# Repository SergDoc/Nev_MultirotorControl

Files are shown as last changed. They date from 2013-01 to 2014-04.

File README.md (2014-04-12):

Nev_MultirotorControl
=====================
Baseflight (naze32) port to own STM32F4 board

STM32F407VGT6

MPU6000 on SPI

HMC5883

MS5611

50x50mm 2 layer pcb, 45mm mounting pattern 

8 + 12 PWM I/O  input or output for RC/CPPM/Motors/Servos 

8 channel standard PWM RC input 

PWM (50..1kHz) motor output for up to 12 motors, 8 motors + 4 Servos

Onboard USB connector 

3 UART accessible for telemetry,  firmware update,  Spektrum Satellite RX or GPS

Battery voltage monitoring and low-voltage alarm 

Buzzer for alarm/user notification 

4 Status LEDs

2 VDD & VCC Status LEDs



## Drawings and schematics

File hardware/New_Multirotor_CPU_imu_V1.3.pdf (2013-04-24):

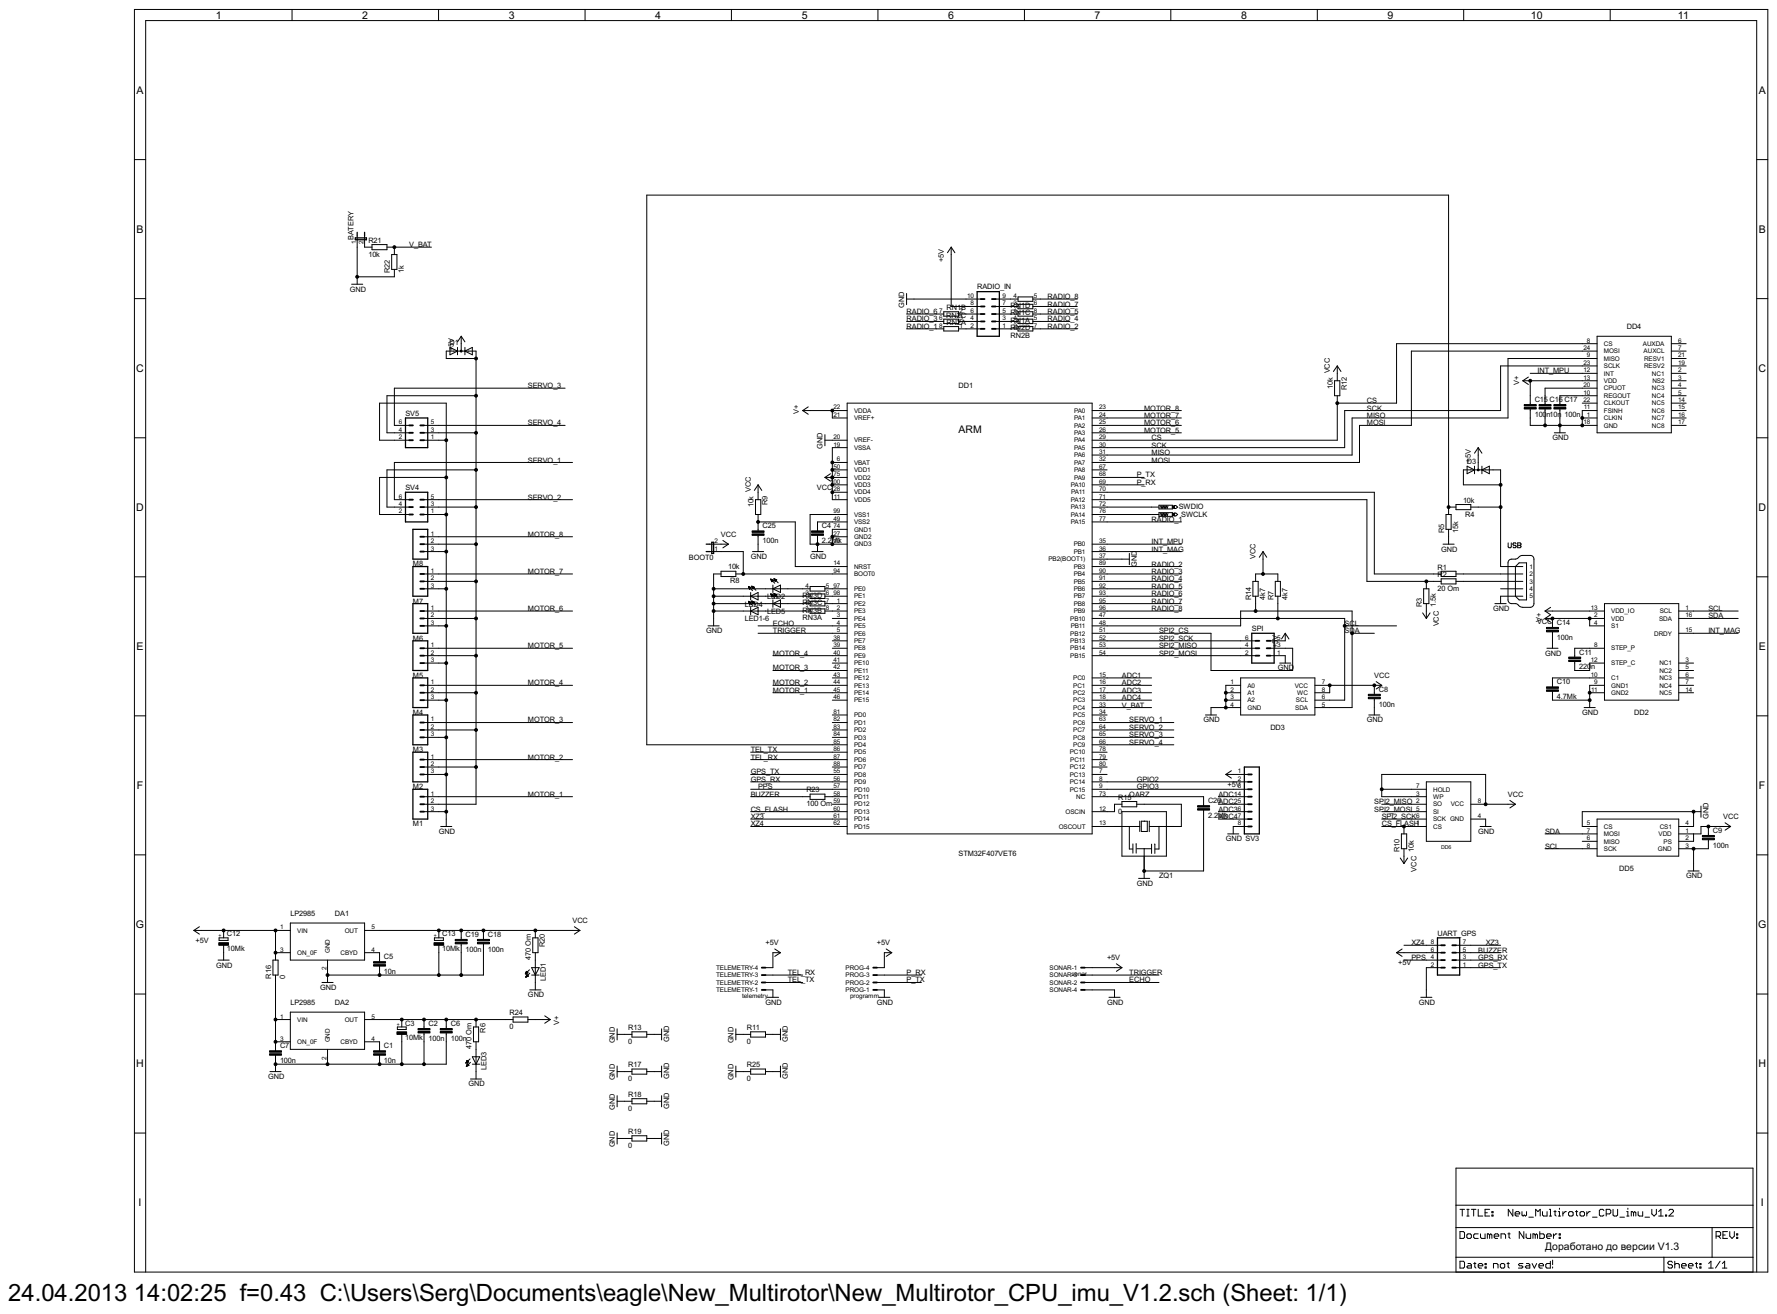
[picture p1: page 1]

C4 | 76 PA15 77 PB0 RADIO_1 35 PB1 INT_MPU

52 PB14 SPI2_MISO | 4 | 3
53 PB15 SPI2_MOSI | 2

PROG-1 PROG-2 PROG-3 PROG-4

24.04.2013 14:02:25 f=0.43 C:\Users\Serg\Documents\eagle\New_Multirotor\New_Multirotor_CPU_imu_V1.2.sch (Sheet: 1/1)

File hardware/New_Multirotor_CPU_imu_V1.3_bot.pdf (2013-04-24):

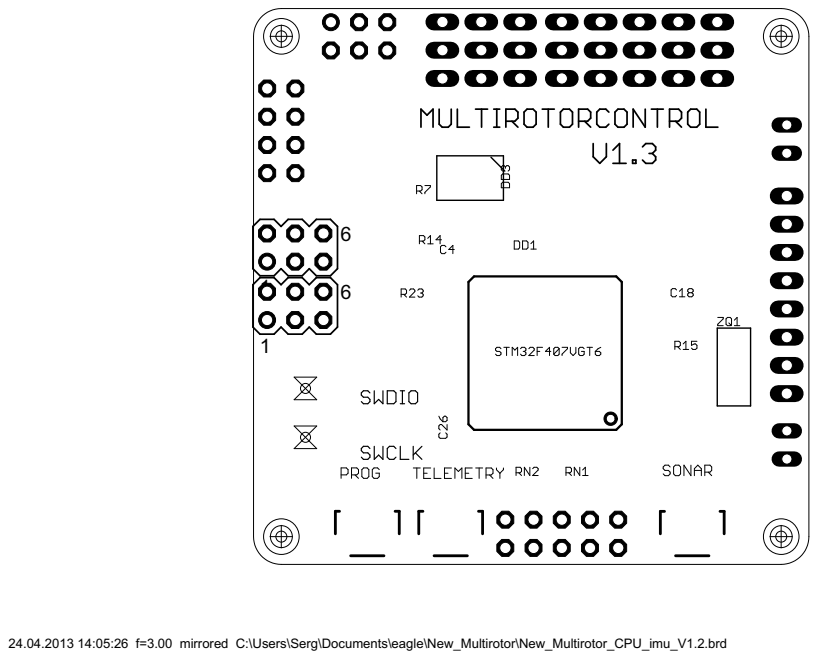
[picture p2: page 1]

24.04.2013 14:05:26 f=3.00 mirrored C:\Users\Serg\Documents\eagle\New_Multirotor\New_Multirotor_CPU_imu_V1.2.brd

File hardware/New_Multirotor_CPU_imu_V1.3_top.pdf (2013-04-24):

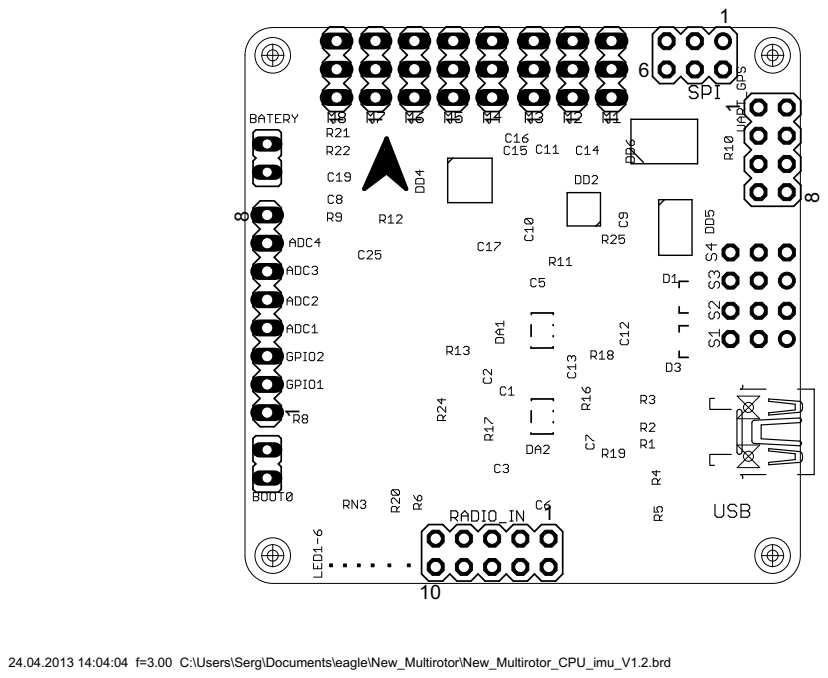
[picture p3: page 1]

24.04.2013 14:04:04 f=3.00 C:\Users\Serg\Documents\eagle\New_Multirotor\New_Multirotor_CPU_imu_V1.2.brd

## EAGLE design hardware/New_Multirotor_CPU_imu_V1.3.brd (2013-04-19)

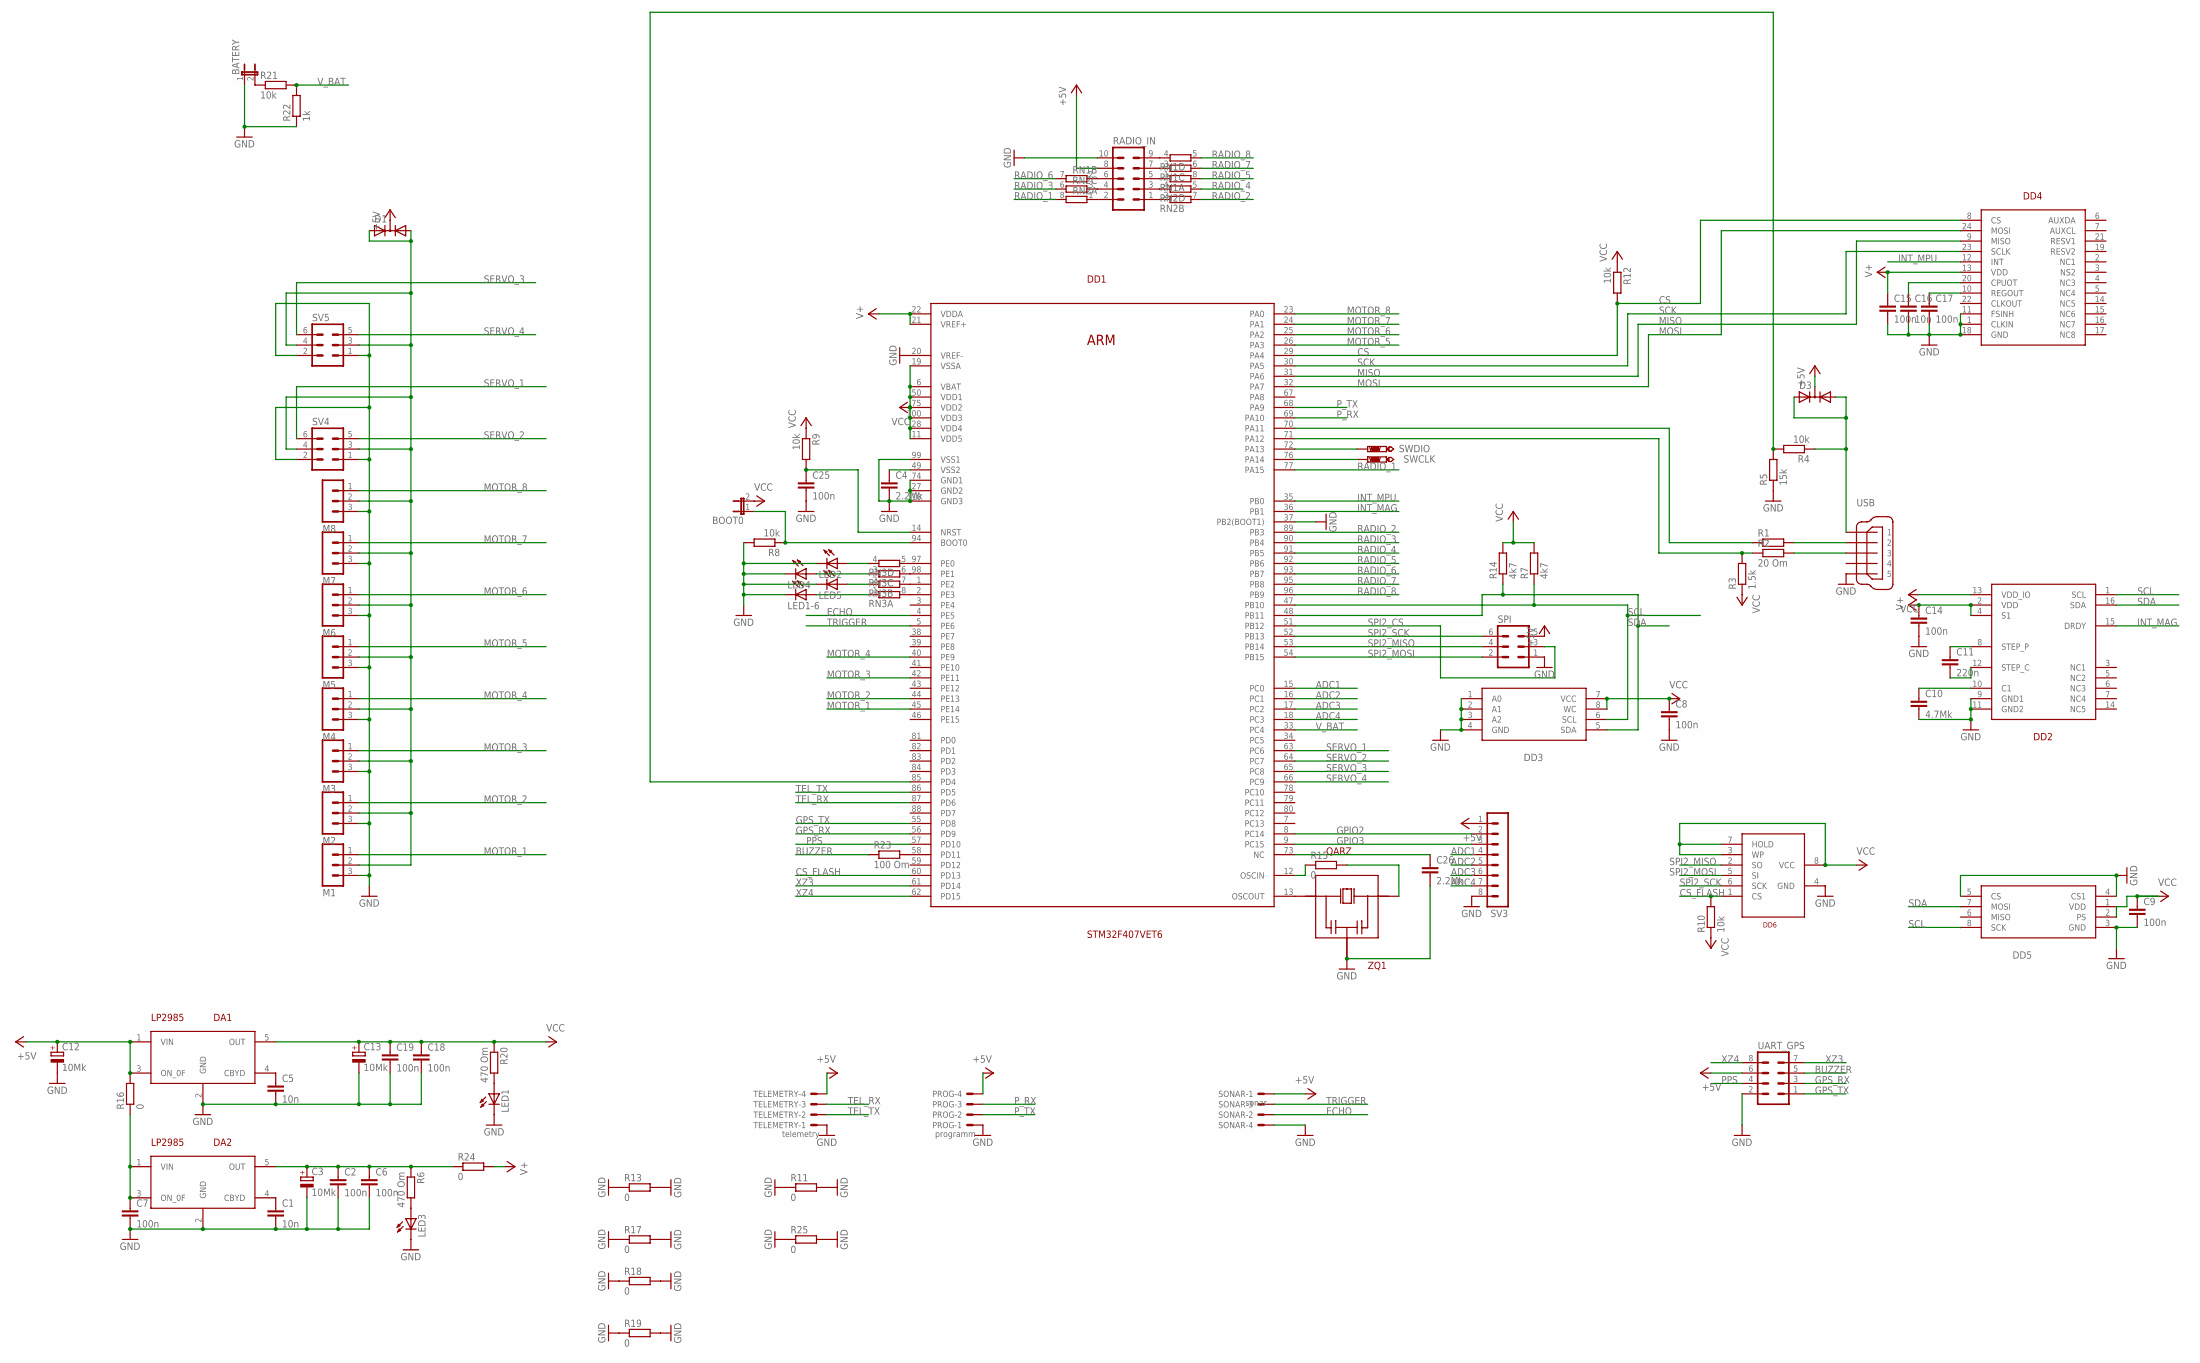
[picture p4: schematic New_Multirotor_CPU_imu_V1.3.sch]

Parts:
BATERY: JP1E; JP1
BOOT0: JP1E; JP1
C1, C5, C16: 10n; C0603K
C2, C6, C7, C8, C9, C14, C15, C17, C18, C19, C25: 100n; C0603K
C3, C12, C13: 10Mk; A/3216-18W
C4, C26: 2.2Mk; C0603K
C10: 4.7Mk; C0603K
C11: 220n; C0603K
D1, D3: DIODE-2AC|CASOT23; SOT23
DA1, DA2: LP2985; SOT23-5L
DD1: STM32F407VET6; LQFP100
DD2: HMC5883L; LCC-16
DD3: 24C512; SOIC8
DD4: MPU6000; JEDEC
DD5: MS5611-01BA03
DD6: W25X40; SOIC8
LED1, LED1-6, LED2, LED3, LED4, LED5: LEDCHIPLED_0603; CHIPLED_0603
M1, M2, M3, M4, M5, M6, M7, M8: MA03-1
PROG: programm; SM04B-SRSS-TB
R1: R-EU_R0603; R0603
R2: 20 Om; R0603
R3: 1.5k; R0603
R4, R8, R9, R10, R12, R21: 10k; R0603
R5: 15k; R0603
R6, R20: 470 Om; R0603
R7, R14: 4k7; R0603
R11, R13, R15, R16, R17, R18, R19, R24, R25: 0; R0603
R22: 1k; R0603
R23: 100 Om; R0603
RADIO_IN: MA05-2
RN1, RN2, RN3: 4R-N0603-ARV; 0603-ARV
SONAR: sonar; SM04B-SRSS-TB
SPI: MA03-2
SV3: MA08-1
SV4, SV5: MA03-2
SWCLK: PTR1TP12R; TP12R
SWDIO: PTR1TP12R; TP12R
TELEMETRY: telemetry; SM04B-SRSS-TB
UART_GPS: MA04-2
USB: 32005-201
ZQ1: QARZ

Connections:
+5V: C12.+, D1.3 (C), D3.3 (C), DA1.1 (VIN), DA1.3 (ON_0F), PROG.4, R16.2, RADIO_IN.8, SONAR.1, SPI.5, SV3.1, TELEMETRY.4, UART_GPS.6
ADC1: DD1.15 (PC0), SV3.4
ADC2: DD1.16 (PC1), SV3.5
ADC3: DD1.17 (PC2), SV3.6
ADC4: DD1.18 (PC3), SV3.7
BUZZER: R23.1, UART_GPS.5
CS: DD1.29 (PA4), DD4.8 (CS), R12.2
CS_FLASH: DD1.60 (PD13), DD6.1 (CS), R10.2
ECHO: DD1.4 (PE5), SONAR.2
GND: BATERY.1, C1.2, C2.2, C3.-, C4.2, C5.2, C6.2, C7.2, C8.2, C9.2, C10.2, C12.-, C13.-, C14.2, C15.2, C16.2, C17.2, C18.2, C19.2, C25.2, C26.2, DA1.2 (GND), DA2.2 (GND), DD1.10 (GND3), DD1.20 (VREF-), DD1.27 (GND2), DD1.37 (PB2(BOOT1)), DD1.74 (GND1), DD1.99 (VSS1), DD2.9 (GND1), DD2.11 (GND2), DD3.1 (A0), DD3.2 (A1), DD3.3 (A2), DD3.4 (GND), DD4.1 (CLKIN), DD4.11 (FSINH), DD4.18 (GND), DD5.3 (GND), DD5.4 (CS1), DD5.5 (CS), DD6.4 (GND), LED1.C, LED1-6.C, LED2.C, LED3.C, LED4.C, LED5.C, M1.3, M2.3, M3.3, M4.3, M5.3, M6.3, M7.3, M8.3, PROG.1, R5.1, R8.2, R11.1, R11.2, R13.1, R13.2, R17.1, R17.2, R18.1, R18.2, R19.1, R19.2, R22.1, R25.1, R25.2, RADIO_IN.10, SONAR.4, SPI.1, SV3.8, SV4.1, SV4.2, SV5.1, SV5.2, TELEMETRY.1, UART_GPS.2, USB.5, ZQ1.2
GPIO2: DD1.8 (PC14), SV3.2
GPIO3: DD1.9 (PC15), SV3.3
GPS_RX: DD1.56 (PD9), UART_GPS.3
GPS_TX: DD1.55 (PD8), UART_GPS.1
INT_MAG: DD1.36 (PB1), DD2.15 (DRDY)
INT_MPU: DD1.35 (PB0), DD4.12 (INT)
MISO: DD1.31 (PA6), DD4.9 (MISO)
MOSI: DD1.32 (PA7), DD4.24 (MOSI)
MOTOR_1: DD1.45 (PE14), M1.1
MOTOR_2: DD1.44 (PE13), M2.1
MOTOR_3: DD1.42 (PE11), M3.1
MOTOR_4: DD1.40 (PE9), M4.1
MOTOR_5: DD1.26 (PA3), M5.1
MOTOR_6: DD1.25 (PA2), M6.1
MOTOR_7: DD1.24 (PA1), M7.1
MOTOR_8: DD1.23 (PA0), M8.1
unnamed: DD1.13 (OSCOUT), ZQ1.1
unnamed: R15.2, ZQ1.3
unnamed: DD1.97 (PE0), RN3.5 (2)
unnamed: C1.1, DA2.4 (CBYD)
unnamed: DD1.98 (PE1), RN3.6 (2)
unnamed: LED3.A, R6.2
unnamed: C2.1, C3.+, C6.1, DA2.5 (OUT), R6.1, R24.1
unnamed: RADIO_IN.5, RN1.1
unnamed: C7.1, DA2.1 (VIN), DA2.3 (ON_0F), R16.1
unnamed: DD1.1 (PE2), RN3.7 (2)
unnamed: DD1.2 (PE3), RN3.8 (2)
unnamed: DD1.12 (OSCIN), R15.1
unnamed: LED1.A, R20.2
unnamed: DD1.72 (PA13), SWDIO.TP
unnamed: DD1.76 (PA14), SWCLK.TP
unnamed: LED2.A, RN3.4 (1)
unnamed: LED4.A, RN3.3 (1)
unnamed: C16.1, DD4.20 (CPUOT)
unnamed: D1.1 (A1), D1.2 (A2), M1.2, M2.2, M3.2, M4.2, M5.2, M6.2, M7.2, M8.2, SV4.3, SV4.4, SV5.3, SV5.4
unnamed: RADIO_IN.3, RN2.4 (1)
unnamed: C17.1, DD4.10 (REGOUT)
unnamed: RADIO_IN.9, RN1.4 (1)
unnamed: RADIO_IN.7, RN1.3 (1)
unnamed: BATERY.2, R21.1
unnamed: C10.1, DD2.10 (C1)
unnamed: C11.2, DD2.12 (STEP_C)
unnamed: C11.1, DD2.8 (STEP_P)
unnamed: DD1.58 (PD11), R23.2
unnamed: RADIO_IN.6, RN1.2 (1)
unnamed: RADIO_IN.1, RN2.2 (1)
unnamed: RADIO_IN.4, RN2.3 (1)
unnamed: RADIO_IN.2, RN2.1
unnamed: LED5.A, RN3.2 (1)
unnamed: LED1-6.A, RN3.1
unnamed: DD1.70 (PA11), R1.1
unnamed: DD1.71 (PA12), R2.1, R3.2
unnamed: R1.2, USB.2
unnamed: R2.2, USB.3
unnamed: DD1.85 (PD4), R4.2, R5.2
unnamed: D3.1 (A1), D3.2 (A2), R4.1, USB.1
unnamed: C5.1, DA1.4 (CBYD)
unnamed: C4.1, DD1.49 (VSS2)
unnamed: BOOT0.1, DD1.94 (BOOT0), R8.1
unnamed: C25.1, DD1.14 (NRST), R9.2
unnamed: C26.1, DD1.73 (NC)
PPS: DD1.57 (PD10), UART_GPS.4
P_RX: DD1.69 (PA10), PROG.3
P_TX: DD1.68 (PA9), PROG.2
RADIO_1: DD1.77 (PA15), RN2.8 (2)
RADIO_2: DD1.89 (PB3), RN2.7 (2)
RADIO_3: DD1.90 (PB4), RN2.6 (2)
RADIO_4: DD1.91 (PB5), RN2.5 (2)
RADIO_5: DD1.92 (PB6), RN1.8 (2)
RADIO_6: DD1.93 (PB7), RN1.7 (2)
RADIO_7: DD1.95 (PB8), RN1.6 (2)
RADIO_8: DD1.96 (PB9), RN1.5 (2)
SCK: DD1.30 (PA5), DD4.23 (SCLK)
SCL: DD1.47 (PB10), DD2.1 (SCL), DD3.6 (SCL), DD5.8 (SCK), R7.1
SDA: DD1.48 (PB11), DD2.16 (SDA), DD3.5 (SDA), DD5.7 (MOSI), R14.1
SERVO_1: DD1.63 (PC6), SV4.6
SERVO_2: DD1.64 (PC7), SV4.5
SERVO_3: DD1.65 (PC8), SV5.6
SERVO_4: DD1.66 (PC9), SV5.5
SPI2_CS: DD1.51 (PB12), SPI.3
SPI2_MISO: DD1.53 (PB14), DD6.2 (SO), SPI.4
SPI2_MOSI: DD1.54 (PB15), DD6.5 (SI), SPI.2
SPI2_SCK: DD1.52 (PB13), DD6.6 (SCK), SPI.6
TEL_RX: DD1.87 (PD6), TELEMETRY.3
TEL_TX: DD1.86 (PD5), TELEMETRY.2
TRIGGER: DD1.5 (PE6), SONAR.3
V+: C14.1, C15.1, DD1.21 (VREF+), DD1.22 (VDDA), DD2.2 (VDD), DD2.4 (S1), DD4.13 (VDD), R24.2
VCC: BOOT0.2, C8.1, C9.1, C13.+, C18.1, C19.1, DA1.5 (OUT), DD1.6 (VBAT), DD1.11 (VDD5), DD1.19 (VSSA), DD1.28 (VDD4), DD1.50 (VDD1), DD1.75 (VDD2), DD1.100 (VDD3), DD2.13 (VDD_IO), DD3.7 (VCC), DD3.8 (WC), DD5.1 (VDD), DD5.2 (PS), DD6.3 (WP), DD6.7 (HOLD), DD6.8 (VCC), R3.1, R7.2, R9.1, R10.1, R12.1, R14.2, R20.1
V_BAT: DD1.33 (PC4), R21.2, R22.2
XZ3: DD1.61 (PD14), UART_GPS.7
XZ4: DD1.62 (PD15), UART_GPS.8

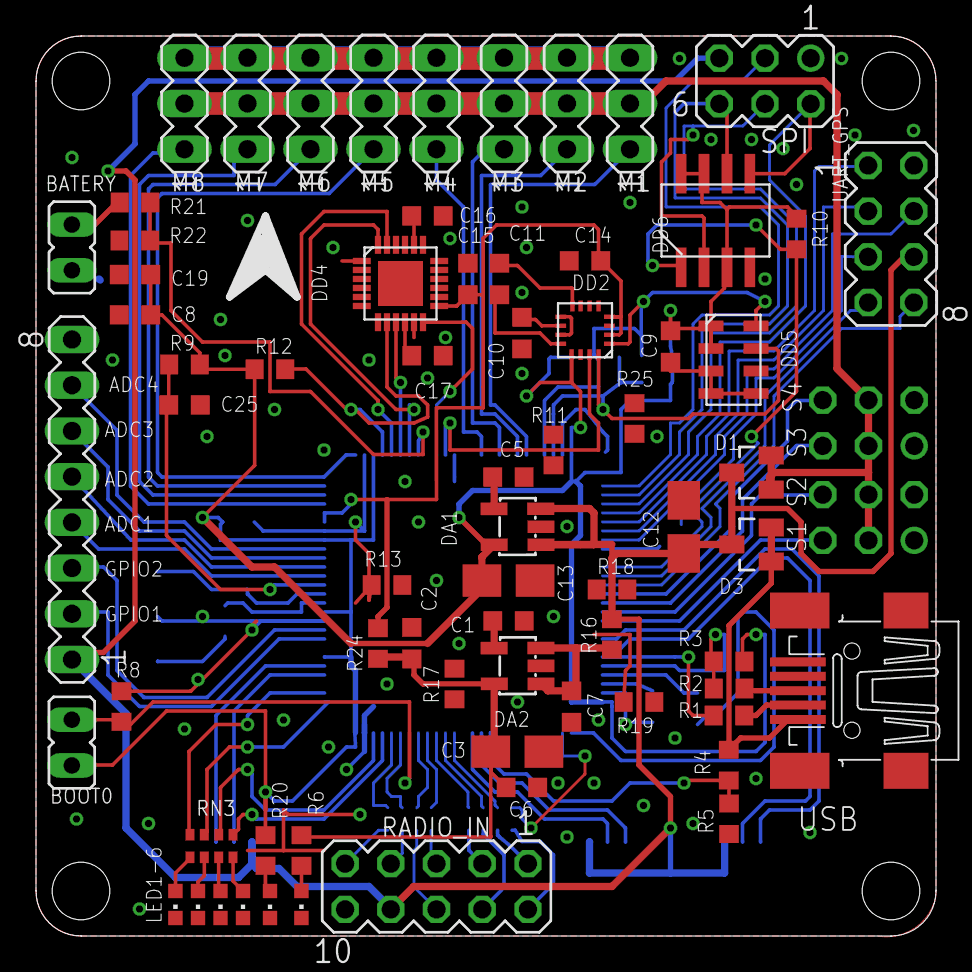
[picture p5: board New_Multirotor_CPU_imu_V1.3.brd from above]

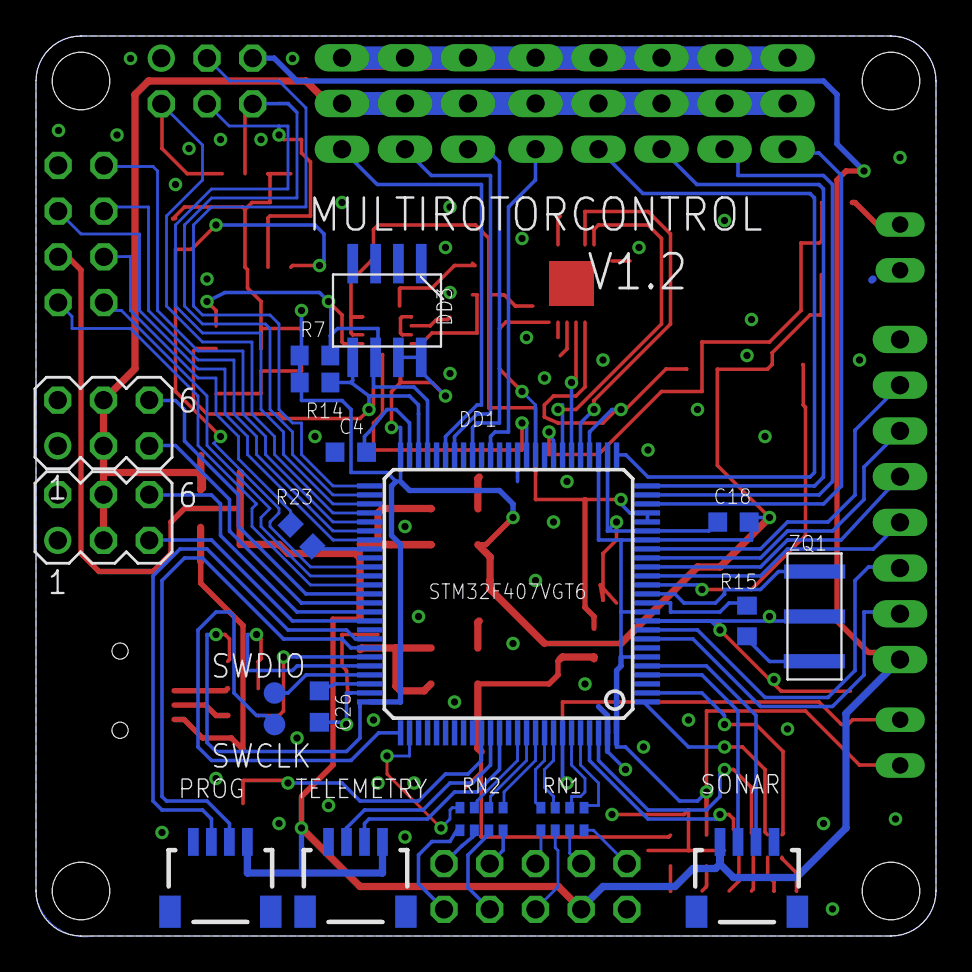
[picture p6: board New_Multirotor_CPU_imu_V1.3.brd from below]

Board: 2 copper layers, 50.0 x 50.0 mm, 88 parts (19 on the bottom side), 101 nets.

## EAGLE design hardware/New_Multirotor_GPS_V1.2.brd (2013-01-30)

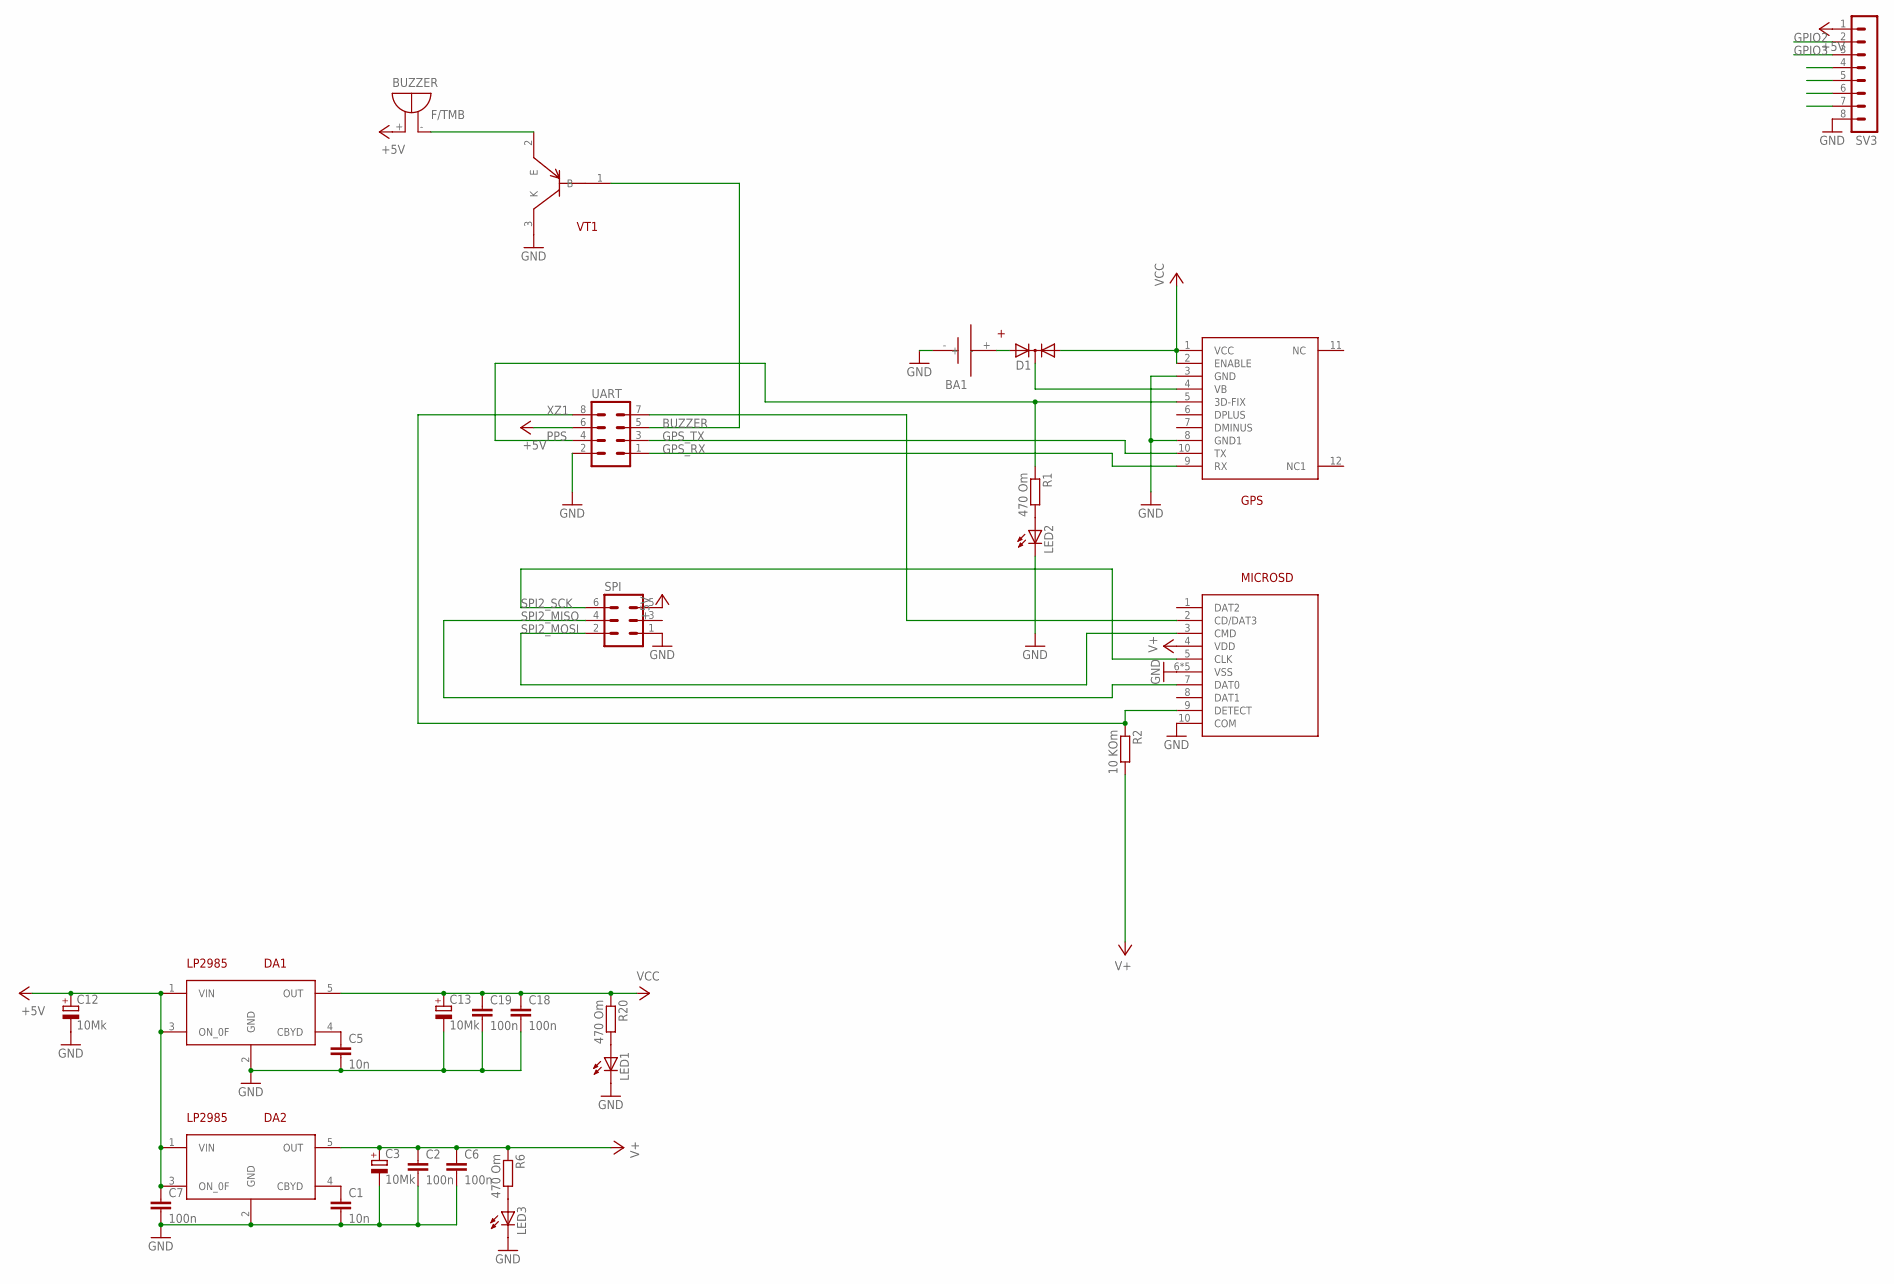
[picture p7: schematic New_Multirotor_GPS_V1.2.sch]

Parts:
BA1: BAT
BUZZER: F/TMB
C1, C5: 10n; C0603K
C2, C6, C7, C18, C19: 100n; C0603K
C3, C12, C13: 10Mk; A/3216-18W
D1: DIODE-2AC|CASOT23; SOT23
DA1, DA2: LP2985; SOT23-5L
GPS: FGPMMOPA6B
LED1, LED2, LED3: LEDCHIPLED_0603; CHIPLED_0603
MICROSD: MICROCD_MAIN; MICROSD_MAIN
R1, R6, R20: 470 Om; R0603
R2: 10 KOm; R0603
SPI: MA03-2
SV3: MA08-1
UART: MA04-2
VT1: MMBT3906; SOT23B-3

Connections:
+5V: BUZZER.+, C7.1, C12.+, DA1.1 (VIN), DA1.3 (ON_0F), DA2.1 (VIN), DA2.3 (ON_0F), SPI.5, SV3.1, UART.6
ADC1: SV3.4
ADC2: SV3.5
ADC3: SV3.6
ADC4: SV3.7
BUZZER: UART.5, VT1.1 (B)
GND: BA1.-, C1.2, C2.2, C3.-, C5.2, C6.2, C7.2, C12.-, C13.-, C18.2, C19.2, DA1.2 (GND), DA2.2 (GND), GPS.3 (GND), GPS.8 (GND1), LED1.C, LED2.C, LED3.C, MICROSD.6 (VSS), MICROSD.10 (COM), MICROSD.11 (VSS), MICROSD.12 (VSS), MICROSD.13 (VSS), MICROSD.14 (VSS), SPI.1, SV3.8, UART.2, VT1.3 (K)
GPIO2: SV3.2
GPIO3: SV3.3
GPS_RX: GPS.9 (RX), UART.1
GPS_TX: GPS.10 (TX), UART.3
unnamed: LED2.A, R1.2
unnamed: BUZZER.-, VT1.2 (E)
unnamed: D1.3 (C), GPS.4 (VB)
unnamed: C1.1, DA2.4 (CBYD)
unnamed: BA1.+, D1.2 (A2)
unnamed: LED3.A, R6.2
unnamed: MICROSD.2 (CD/DAT3), UART.7
unnamed: LED1.A, R20.2
unnamed: C5.1, DA1.4 (CBYD)
PPS: GPS.5 (3D-FIX), R1.1, UART.4
SPI2_MISO: MICROSD.7 (DAT0), SPI.4
SPI2_MOSI: MICROSD.3 (CMD), SPI.2
SPI2_SCK: MICROSD.5 (CLK), SPI.6
V+: C2.1, C3.+, C6.1, DA2.5 (OUT), MICROSD.4 (VDD), R2.2, R6.1
VCC: C13.+, C18.1, C19.1, D1.1 (A1), DA1.5 (OUT), GPS.1 (VCC), GPS.2 (ENABLE), R20.1
XZ1: MICROSD.9 (DETECT), R2.1, UART.8

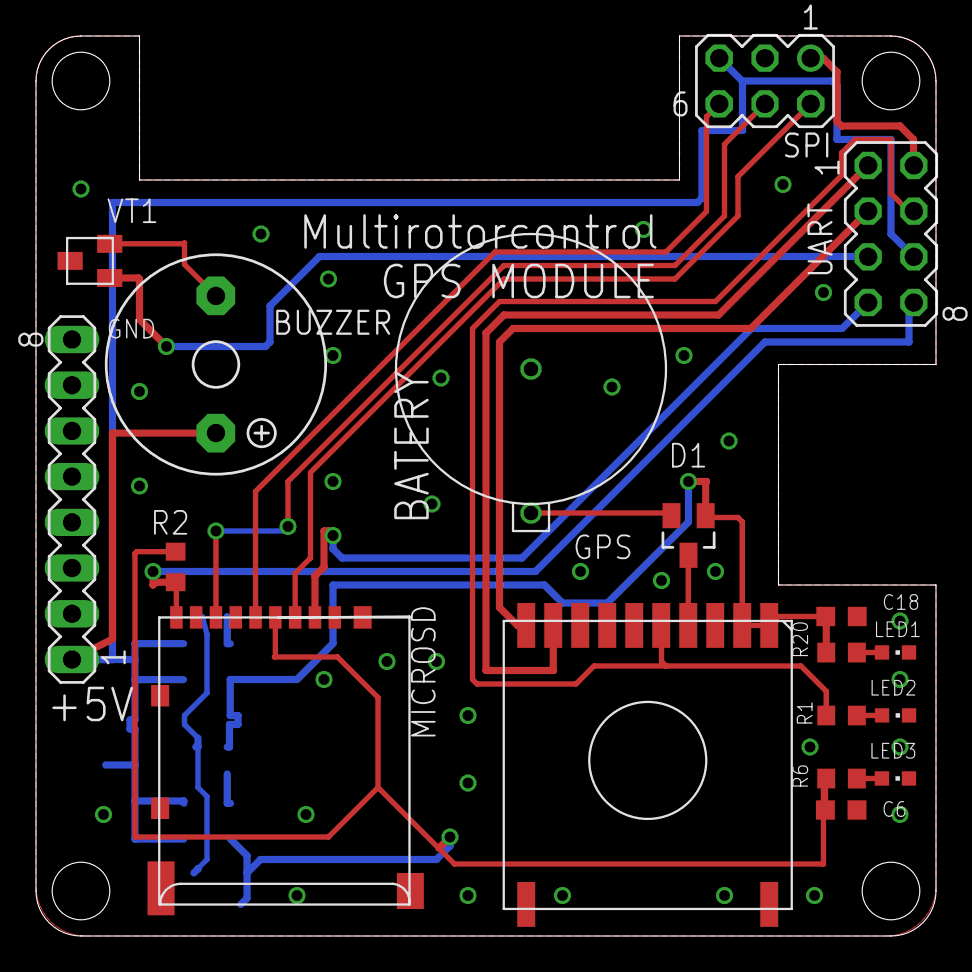
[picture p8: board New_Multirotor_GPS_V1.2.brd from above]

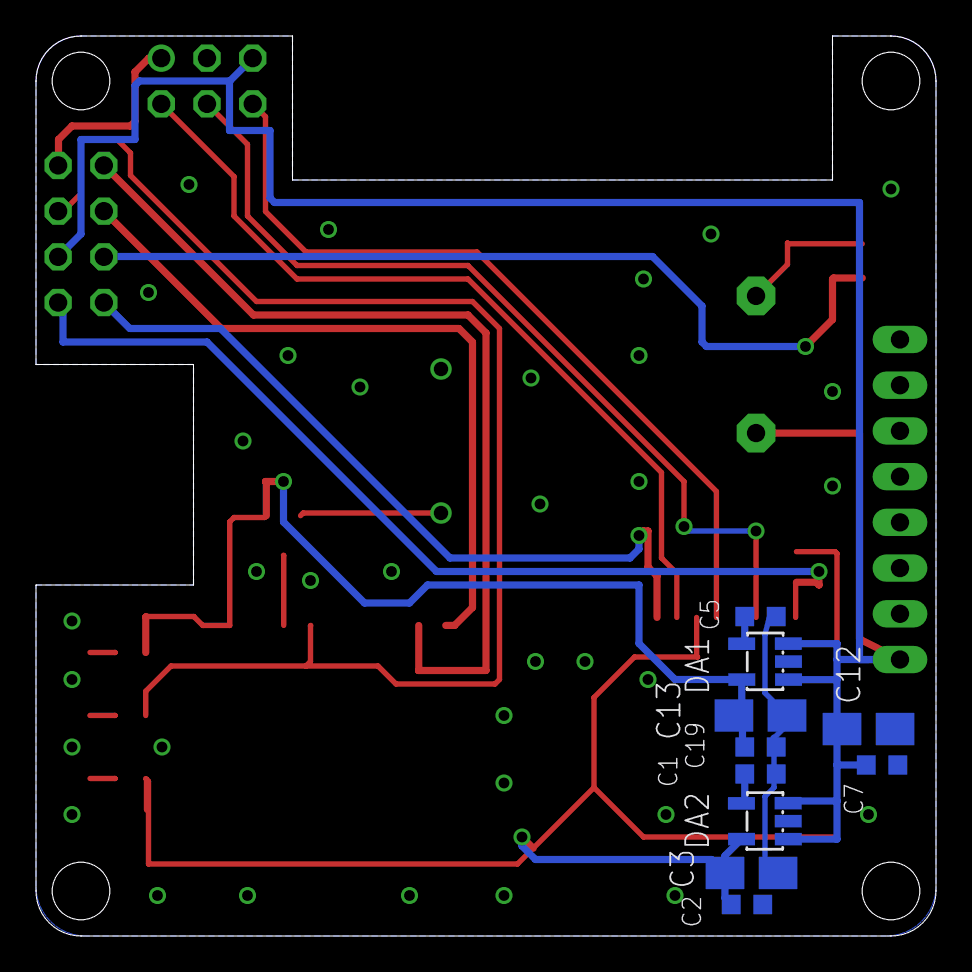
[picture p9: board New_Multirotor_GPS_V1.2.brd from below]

Board: 2 copper layers, 50.0 x 50.0 mm, 28 parts (10 on the bottom side), 21 nets.

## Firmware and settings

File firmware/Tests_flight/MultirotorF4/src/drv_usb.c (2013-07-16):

#include "drv_usb.h"
#include "board.h"
 
#include "../lib/STM32_USB_Driver/usb_bsp.h"
#include "../lib/STM32_USB_Driver/usb_regs.h"
#include "../lib/STM32_USB_Driver/usbd_conf.h"
#include "../lib/STM32_USB_Driver/usbd_usr.h"
#include "../lib/STM32_USB_Driver/usbd_desc.h"
#include "../lib/STM32_USB_Driver/usbd_cdc_core.h"
#include "../lib/STM32_USB_Driver/usbd_ioreq.h"
#include "../lib/STM32_USB_Driver/usbd_req.h"
#include "../lib/STM32_USB_Driver/usbd_core.h"



typedef uint8_t U8;
typedef uint32_t U32;
typedef uint16_t U16;

#define USBD_MANUFACTURER_STRING        "IBEGlab"
#define USBD_PRODUCT_FS_STRING          "IBEG Virtual COM"
#define USBD_SERIALNUMBER_FS_STRING     "00000000050C"
#define USBD_CONFIGURATION_FS_STRING    "VCP Config"
#define USBD_INTERFACE_FS_STRING        "VCP Interface"

#define USBD_VID                        0x0483
#define USBD_PID                        0x5740
#define USBD_LANGID_STRING              0x409

#define USB_RXFIFO_SIZE 256
#define USB_TXFIFO_SIZE 256

extern USB_OTG_CORE_HANDLE           USB_OTG_dev;
extern uint32_t USBD_OTG_ISR_Handler (USB_OTG_CORE_HANDLE *pdev);

__ALIGN_BEGIN USB_OTG_CORE_HANDLE  USB_OTG_dev __ALIGN_END;

static usb_attr_t *usb_attr;
static U8 usb_connected;

static const U16 rxfifo_size = USB_RXFIFO_SIZE;
static const U16 txfifo_size = USB_TXFIFO_SIZE;

static ring_buffer _rxfifo;
static ring_buffer _txfifo;

static ring_buffer *rxfifo = &_rxfifo;                /* Rx FIFO */
static ring_buffer *txfifo = &_txfifo;                /* Rx FIFO */

static uint8_t rx_buf[USB_RXFIFO_SIZE];
static uint8_t tx_buf[USB_TXFIFO_SIZE];

static U8 preempt_prio, sub_prio;
static U8 usb_ready;

LINE_CODING linecoding =
  {
    115200, /* baud rate*/
    0x00,   /* stop bits-1*/
    0x00,   /* parity - none*/
    0x08    /* nb. of bits 8*/
  };
	
/* These are external variables imported from CDC core to be used for IN 
   transfer management. */
extern U8  APP_Rx_Buffer []; /* Write CDC received data in this buffer.
                                These data will be sent over USB IN endpoint
                                in the CDC core functions. */
extern U32 APP_Rx_ptr_in;    /* Increment this pointer or roll it back to
                                start address when writing received data
                                in the buffer APP_Rx_Buffer. */

/* Private function prototypes -----------------------------------------------*/
static U16 VCP_Init     (void);
static U16 VCP_DeInit   (void);
static U16 VCP_Ctrl     (uint32_t Cmd, uint8_t* Buf, uint32_t Len);
static U16 VCP_DataTx   (uint8_t* Buf, uint32_t Len);
static U16 VCP_DataRx   (uint8_t* Buf, uint32_t Len);

CDC_IF_Prop_TypeDef VCP_fops = 
{
  VCP_Init,
  VCP_DeInit,
  VCP_Ctrl,
  VCP_DataTx,
  VCP_DataRx
};

USBD_Usr_cb_TypeDef USR_cb =
{
  USBD_USR_Init,
  USBD_USR_DeviceReset,
  USBD_USR_DeviceConfigured,
  USBD_USR_DeviceSuspended,
  USBD_USR_DeviceResumed,
  USBD_USR_DeviceConnected,
  USBD_USR_DeviceDisconnected,
};


USBD_DEVICE USR_desc =
{
  USBD_USR_DeviceDescriptor,
  USBD_USR_LangIDStrDescriptor, 
  USBD_USR_ManufacturerStrDescriptor,
  USBD_USR_ProductStrDescriptor,
  USBD_USR_SerialStrDescriptor,
  USBD_USR_ConfigStrDescriptor,
  USBD_USR_InterfaceStrDescriptor,
  
};

/* USB Standard Device Descriptor */
__ALIGN_BEGIN U8 USBD_DeviceDesc[USB_SIZ_DEVICE_DESC] __ALIGN_END =
  {
    0x12,                       /*bLength */
    USB_DEVICE_DESCRIPTOR_TYPE, /*bDescriptorType*/
    0x00,                       /*bcdUSB */
    0x02,
    0x00,                       /*bDeviceClass*/
    0x00,                       /*bDeviceSubClass*/
    0x00,                       /*bDeviceProtocol*/
    USB_OTG_MAX_EP0_SIZE,      /*bMaxPacketSize*/
    LOBYTE(USBD_VID),           /*idVendor*/
    HIBYTE(USBD_VID),           /*idVendor*/
    LOBYTE(USBD_PID),           /*idVendor*/
    HIBYTE(USBD_PID),           /*idVendor*/
    0x00,                       /*bcdDevice rel. 2.00*/
    0x02,
    USBD_IDX_MFC_STR,           /*Index of manufacturer  string*/
    USBD_IDX_PRODUCT_STR,       /*Index of product string*/
    USBD_IDX_SERIAL_STR,        /*Index of serial number string*/
    USBD_CFG_MAX_NUM            /*bNumConfigurations*/
  } ; /* USB_DeviceDescriptor */

/* USB Standard Device Descriptor */
__ALIGN_BEGIN U8 USBD_DeviceQualifierDesc[USB_LEN_DEV_QUALIFIER_DESC] __ALIGN_END =
{
  USB_LEN_DEV_QUALIFIER_DESC,
  USB_DESC_TYPE_DEVICE_QUALIFIER,
  0x00,
  0x02,
  0x00,
  0x00,
  0x00,
  0x40,
  0x01,
  0x00,
};

/* USB Standard Device Descriptor */
__ALIGN_BEGIN U8 USBD_LangIDDesc[USB_SIZ_STRING_LANGID] __ALIGN_END =
{
     USB_SIZ_STRING_LANGID,         
     USB_DESC_TYPE_STRING,       
     LOBYTE(USBD_LANGID_STRING),
     HIBYTE(USBD_LANGID_STRING), 
};


/* Return the device descriptor */
U8 * USBD_USR_DeviceDescriptor(U8 speed, U16 *length)
{
  *length = sizeof(USBD_DeviceDesc);
  return USBD_DeviceDesc;
}

/* return the LangID string descriptor */
U8 * USBD_USR_LangIDStrDescriptor(U8 speed, U16 *length)
{
  *length =  sizeof(USBD_LangIDDesc);  
  return USBD_LangIDDesc;
}



/* return the product string descriptor */
U8 * USBD_USR_ProductStrDescriptor(U8 speed, U16 *length)
{
#ifdef USB_DEBUG
	usart_putstr(_USART1, "desc\n");
#endif
	if (usb_attr && usb_attr->description)
		USBD_GetString ((U8 *)usb_attr->description, USBD_StrDesc, length);
	else
		USBD_GetString ((U8 *)USBD_PRODUCT_FS_STRING, USBD_StrDesc, length);
#ifdef USB_DEBUG
	usart_putstr(_USART1, "desc ok\n");
#endif

return USBD_StrDesc;
}

/* return the manufacturer string descriptor */
U8 * USBD_USR_ManufacturerStrDescriptor(U8 speed, U16 *length)
{

	if (usb_attr && usb_attr->manufacturer)
		USBD_GetString ((U8 *)usb_attr->manufacturer, USBD_StrDesc, length);
	else
		USBD_GetString ((U8 *)USBD_MANUFACTURER_STRING, USBD_StrDesc, length);

return USBD_StrDesc;
}

/* return the serial number string descriptor */
U8 *  USBD_USR_SerialStrDescriptor(U8 speed, U16 *length)
{

	if (usb_attr && usb_attr->serial_number)
		USBD_GetString ((U8 *)usb_attr->serial_number, USBD_StrDesc, length);
	else
		USBD_GetString ((U8 *)USBD_SERIALNUMBER_FS_STRING, USBD_StrDesc, length);

return USBD_StrDesc;
}

/* return the configuration string descriptor */
U8 * USBD_USR_ConfigStrDescriptor(U8 speed , U16 *length)
{

    if (usb_attr && usb_attr->configuration)
		USBD_GetString ((U8 *)usb_attr->configuration, USBD_StrDesc, length);
	else	
		USBD_GetString ((U8 *)USBD_CONFIGURATION_FS_STRING, USBD_StrDesc, length); 

    return USBD_StrDesc;
}


/* return the interface string descriptor */
U8 * USBD_USR_InterfaceStrDescriptor( U8 speed , U16 *length)
{

	if (usb_attr && usb_attr->interface)
		USBD_GetString ((U8 *)usb_attr->interface, USBD_StrDesc, length);
	else	
		USBD_GetString ((U8 *)USBD_INTERFACE_FS_STRING, USBD_StrDesc, length);

return USBD_StrDesc;
}

void USBD_USR_Init(void)
{  

    usb_connected = 0;
}
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

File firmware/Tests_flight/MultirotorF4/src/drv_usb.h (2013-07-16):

#ifndef USB_STM32_H
#define USB_STM32_H

#include <stm32f4xx.h>
#include "ring_buffer.h"
#include <gpio.h>
#include <usart.h>

#define USB_IRQ		OTG_FS_IRQn
#define USB_AF		GPIO_AF_OTG1_FS
#define USB_CLOCK	RCC_AHB2Periph_OTG_FS


/* USB D-/D+ (DM/DP) */
#define DM_PIN_PORT   		_GPIOA  //PA11
#define DM_PIN_PIN   		11
#define DP_PIN_PORT   		_GPIOA  //PA12
#define DP_PIN_PIN   		12  //PA12


/* Exported typef ------------------------------------------------------------*/
/* The following structures groups all needed parameters to be configured for the 
   ComPort. These parameters can modified on the fly by the host through CDC class
   command class requests. */
typedef struct
{
  uint32_t bitrate;
  uint8_t  format;
  uint8_t  paritytype;
  uint8_t  datatype;
} LINE_CODING;

/* USB Attribute Data Structure */
typedef struct {
	uint8_t	preempt_prio;				/* pre-emption priority for the IRQ channel */
	uint8_t	sub_prio;						/* subpriority level for the IRQ channel  */
	uint8_t  use_present_pin;
	gpio_dev *present_port;
	uint16_t present_pin;
	char *description;
	char *manufacturer;
	char *serial_number;
	char *configuration;
	char *interface;
} usb_attr_t;

#define I_USB_CLEAR			1
#define I_USB_CONNECTED		2
#define I_USB_GETATTR		3
#define I_USB_SETATTR		4

#ifdef __cplusplus
  extern "C" {
#endif

/* functions */
int usb_open(void);
int usb_close(void);
int usb_ioctl(int request, void * ctl);
int usb_write(uint8_t *buf, unsigned int nbytes);
int usb_read(void  * buf, unsigned int nbytes);
void usb_default_attr(usb_attr_t *attr);
int usb_configure(usb_attr_t * attr);
int8_t usb_getc(void);
uint32_t usb_data_available(void);
void usb_putc(uint8_t byte);
void usb_reset_rx(void);
void usb_reset_tx(void);

#ifdef __cplusplus
  }
#endif

#endif
/*----------------------------------------------------------------------------
 * end of file
 *---------------------------------------------------------------------------*/

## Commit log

2013-01-19 hardware add
    [New_Multirotor_CPU_imu.brd, New_Multirotor_CPU_imu.sch, New_Multirotor_GPS.brd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]
2013-01-23 Fixes a bug
    [New_Multirotor_CPU_imu.brd, New_Multirotor_CPU_imu.sch]
2013-01-26 Optimized, added the site PA13, PA14 ...
    [New_Multirotor_CPU_imu.brd, New_Multirotor_CPU_imu.sch]
2013-01-27 Перезалил
    [New_Multirotor_CPU_imu.brd, New_Multirotor_CPU_imu.sch]
2013-01-27 Reduced the size to 50x50
    [New_Multirotor_CPU_imu_V1.2.brd, New_Multirotor_CPU_imu_V1.2.sch]
2013-01-28 Add Gerbers files
    [Drills.xln]
2013-01-30 Add GPS board V1.2
    [New_Multirotor_GPS_V1.2.brd, New_Multirotor_GPS_V1.2.sch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]
2013-04-11 Первые признаки жизни
2013-04-11 fixed led bag
2013-04-19 Fixed a bug with baro
    удалил версию 1.2 добавил 1.3...
    [Multirotor.GBL, Multirotor.GBO, Multirotor.GBS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]
2013-04-28 UART + DMA bag :(
    не работает передача tx :(
2013-07-07 New PID added
2013-07-16 fix bag PWM
2013-10-14 Fixed bag DMA
